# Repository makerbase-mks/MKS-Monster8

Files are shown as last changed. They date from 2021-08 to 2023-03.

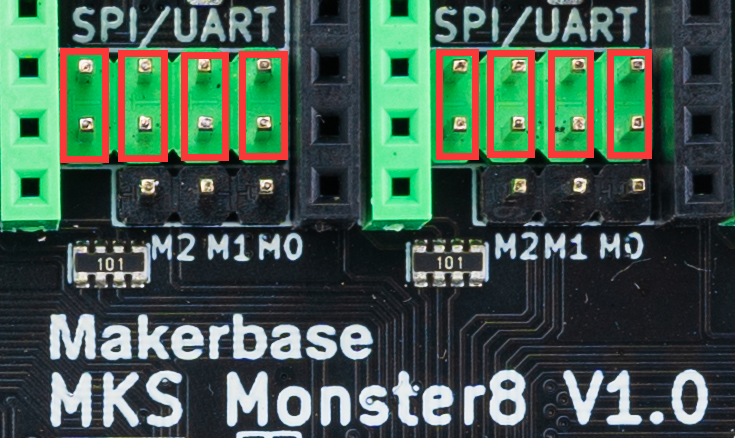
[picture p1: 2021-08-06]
hardware/Image/MKS_Monster8_SPI_set.png

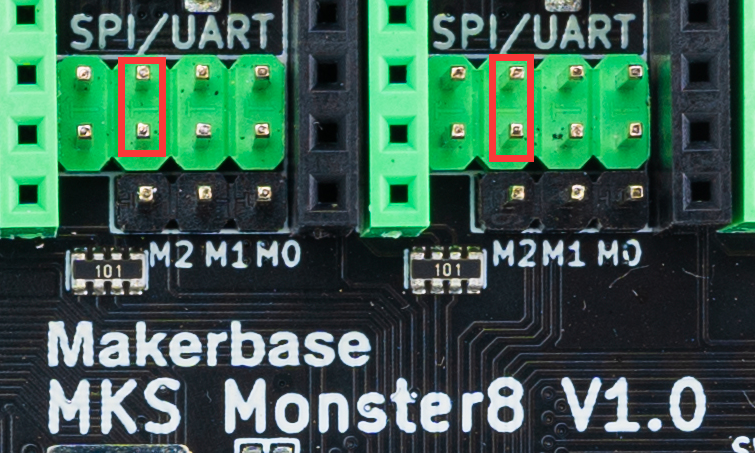
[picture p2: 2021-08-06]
hardware/Image/MKS_Monster8_UART_set.png

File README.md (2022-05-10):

# MKS-Monster8
  Where to buy it?  
  [Monster8 V1 on Aliexpress](https://www.aliexpress.com/item/1005003292898244.html)  
  [Monster8 V2 on Aliexpress](https://www.aliexpress.com/item/1005004241957147.html?spm=a2g0o.store_pc_newArrival.8148356.1.6ecd21f9tROAm6)
  
## Hardware
  - MCU is STM32F407VET6, 168MHz, 512K flash, 192KB RAM
  - DC12-24V input(2 MP1584EN Output DC12V(For FANs) and DC5V)
  - 4 heaters + 4 temps interface(H-BED,HE0,HE1,HE2; TB, TH0,TH1,TH2)
  - 3 PWM FANs + 3 power output(all power can be select by jumper and select VIN, dc12V, dc5V)
  - 8 axis drivers and 9 motor interface(Driver0,1,2-1,2-2,3,4,5,6,7)
  - EXP1,EXP2 support [MKS MINI12864](https://makerbase.aliexpress.com/store/group/LCD/1047297_516922172.html),[MKS TS35](https://www.aliexpress.com/item/1005001446396197.html),LCD12864,LCD2004
  - USART(usart1:PA9,PA10) support [MKS H43](https://www.aliexpress.com/item/1005002008179262.html) or for other serial communication
  - 6 endstop support power select(X-,X+,Y-,Y+,Z-,Z+) and 3D TOUCH(PA8) interface
  - 4K eeprom on board(connect to I2C)
  - Built-in CAN transceiver and interface(connect to CAN)
  - Integrated SPI communication microsd card and reserved SPI signal interface 
  - Integrated UDISK
  - Integrated virtural USB device
  - Support TMC UART and SPI mode, SENSORLESS_HOMING function(Diag0-5,connect to X-,Y-,Z-,X+,Y+,Z+)
  - Support driver power select(5V or 3.3V)
  - Has TVS power spike protection
  - **Possess power reverse connection protection function**
  - Support DFU mode set by button(Boot0)

## Firmware
  - Support Marlin 2.0.x
  - Support Klipper
  - Update firmware
    - DFU upload
	- TF card update
	- Udisk update

## STL files for MKS Monster8 and mini12864 V3.0
You can download from [Github](https://github.com/makerbase-mks/MKS-Monster8/tree/main/STL) or from [Thinkiverse-MKS Monster8](https://www.thingiverse.com/thing:4977292
),[Thinkiverse-MKS Mini12864 V3.0](https://www.thingiverse.com/thing:4918948)
## Related tutorials and Notice
  - MKS Monster8 V1.0 manual, you can refer to Wiki.[click here](https://github.com/makerbase-mks/MKS-Monster8/wiki)
  - MKS Monster8 V2.0 manual, you can refer to Wiki.[click here](https://github.com/makerbase-mks/MKS-Monster8/wiki/MKS_MONSTER8_V2_manual_based_on_Klipper_firmware_to_configure_Voron_2_4_machine)
  - The [marlin 2.0.x firmware](https://github.com/MarlinFirmware/Marlin/tree/bugfix-2.0.x)
  - The [Klipper firmware](https://github.com/KevinOConnor/klipper)
  - [MKS Monster8 klipper firmware bin file](https://github.com/makerbase-mks/Klipper-for-MKS-Boards/tree/main/MKS%20Monster8)

## Note
- Thank you for using MKS products. If you have any questions during use, please contact us in time and we will work with you to solve it.
- For more product dynamic information and tutorial materials, you can always follow MKS's Facebook/Twitter/Discord/Reddit/Youtube and Github. Thank you!
- MKS Github: https://github.com/makerbase-mks  
- MKS Facebook: https://www.facebook.com/Makerbase.mks/  
- MKS Twitter: https://twitter.com/home?lang=en  
- MKS Discord: https://discord.gg/4uar57NEyU
- MKS Reddit: https://www.reddit.com/user/MAKERBASE-TEAM/ 

mks_link

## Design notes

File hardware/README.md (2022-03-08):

# MKS-Monster8-Hardware
- V2.0_003 Version
  - Change it from V2.0_002 Version
  - X-, Y-, Z-, MT-DET interface power only use 5V
  - Z+ power can be select as **VIN** or **5V**, default jump to 5V
  - Version 002 change to 003

- V2.0_002 Version
  - Change it from V1.0_003 version
  - The drive signal is drawn out using the Header 1X4
  - The fuse same as duet2wifi's fuse
  - Endstop, MOS, temperature measurement circuit add schottky diode protection
  - The motor out add Back EMF Protection 
  - X+ pin for MT_DET, Y+ pin for Neopiexl
  - Add MKS Robin Wifi interface
  - E4 axis enable signal same as E0 axis
  - Add MAX31865 interface and the pins use E4 axis
  - Add DC5V 3A out for raspberry pie

- V1.0_003 Version
  - Change it from V1.0_002 version
  - Change D6,D11 packages
  - Power and H-BED interface add silkscreen
  - Optimize U7 design

- V1.0_002 Version
  - Inital version

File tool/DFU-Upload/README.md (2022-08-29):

# MKS-Monster8-DFU
- Upload bootloader
  - Press the Boot0 button when there is no power
  - Connect USB to PC and enter DFU
  - Run: DFU-Upload-Bootloader.bat

- Update firmware
  - Press the Boot0 button when there is no power
  - Connect USB to PC and enter DFU
  - Copy your compiled the mks_monster8.bin file to DFU-Upload path
  - DFU-Upload-firmware.bat
  
- Tips: Can not be modified bootloader's or firmware's file name. Otherwise, DFU cannot be update it.

- More information refer to: https://github.com/makerbase-mks/MKS-Monster8/wiki/DFU_upload

Tip: If your board does not enter the DFU, it may be that the STM32 Bootloar driver is not installed, you can try to run zadig-2.4.exe to install the driver.

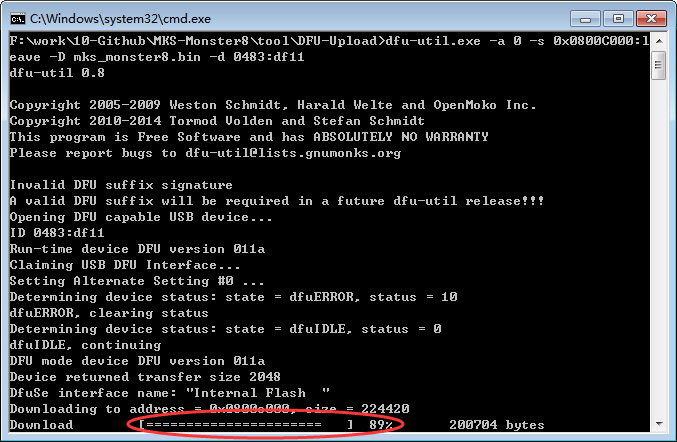
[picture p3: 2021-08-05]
hardware/Image/MKS_Monster8_DFU_upload.png

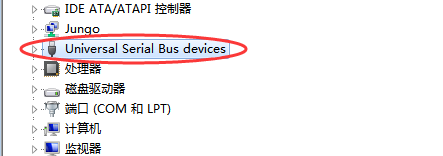
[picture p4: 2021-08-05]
hardware/Image/MKS_Monster8_DFU.png

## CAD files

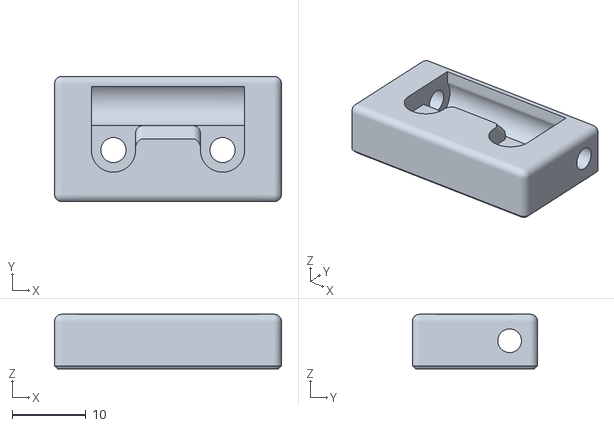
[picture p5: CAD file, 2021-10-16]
STL/MKS Mini12864 V3.0 STL/[a]_mini12864_case_hinge.stl
30.8 x 17.0 x 7.40

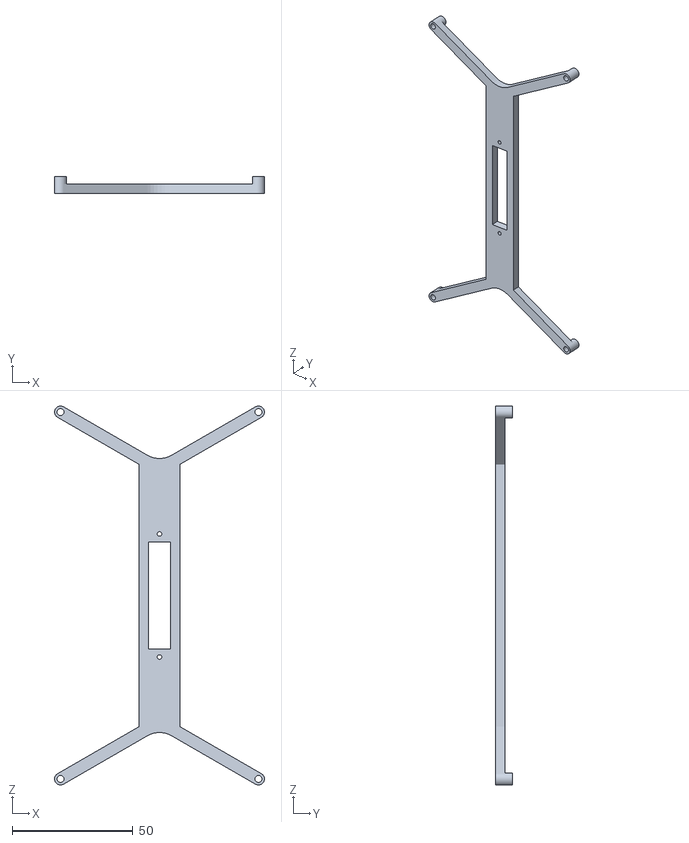
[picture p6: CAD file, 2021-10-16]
STL/MKS Monster8 fixed bracket/Motherboard bracket.STL
87.0 x 7.00 x 157.0

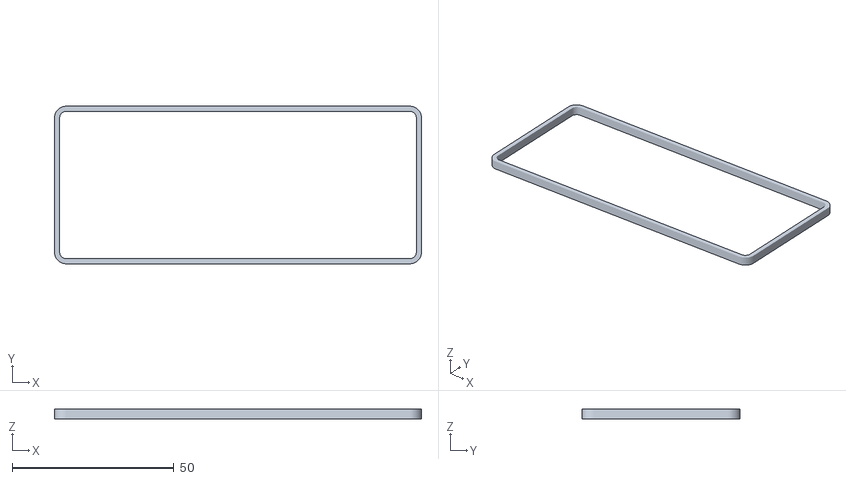
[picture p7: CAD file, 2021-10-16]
STL/MKS Mini12864 V3.0 STL/mini12864_spacer.stl
113.6 x 48.8 x 3.00

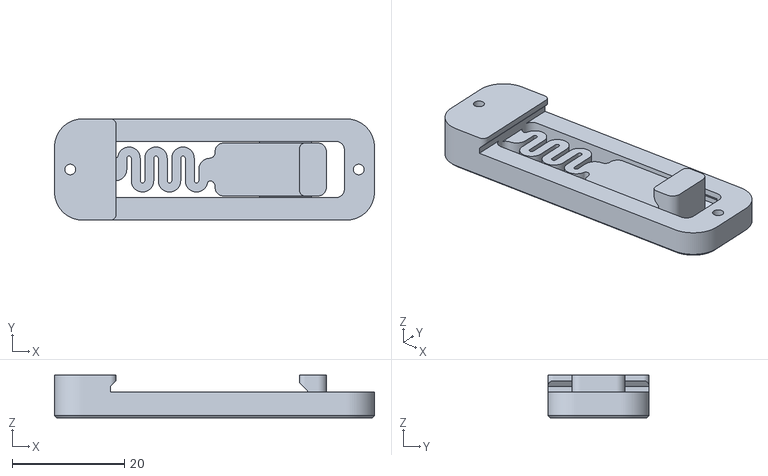
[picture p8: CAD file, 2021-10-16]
STL/MKS Monster8 fixed bracket/pcb_din_clip_x3.stl
56.9 x 18.0 x 7.60

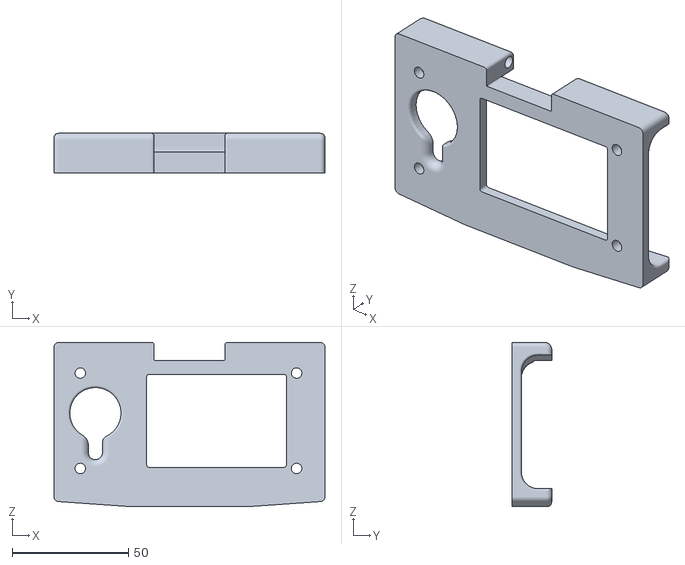
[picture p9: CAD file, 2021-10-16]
STL/MKS Mini12864 V3.0 STL/Upper half.STL
116.5 x 17.0 x 70.6

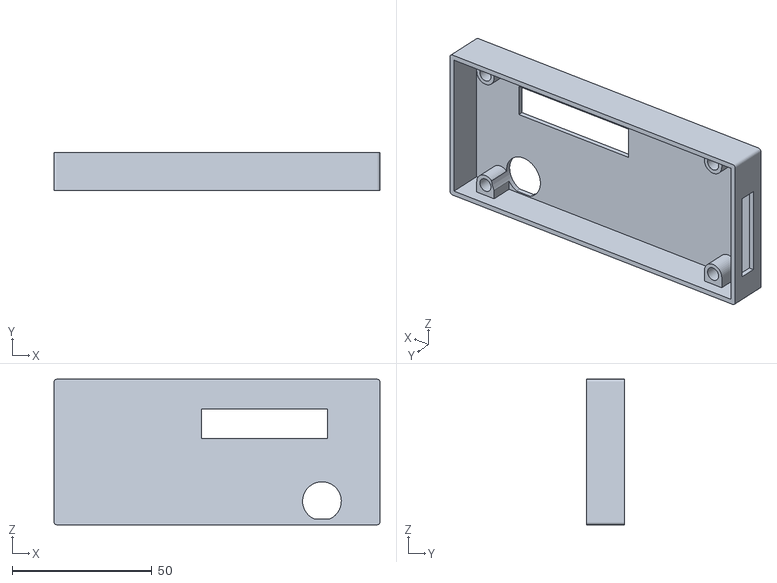
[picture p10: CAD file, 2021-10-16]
STL/MKS Mini12864 V3.0 STL/Bottom half.STL
116.5 x 13.5 x 52.0

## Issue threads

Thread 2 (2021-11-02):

How to connect raspberry?

FabioMiranda10, 2021-11-02:
Is ther a 5v port on the board that supports raspberry pi

mks-viva, 2021-11-05:
I do not recommend that you supply power to the Raspberry Pi directly from the motherboard

mks-viva, 2021-11-19:
V2 has a separate 5V power for raspberry

Diogynes, 2023-06-09:
The V2 5V power supply will not power a Pi over any length of time without under-voltage warnings.  The MP1584E regulator is incapable of sourcing that much current over time.

Closed 2021-11-19.

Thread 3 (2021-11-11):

RRF port support?

whoim2, 2021-11-11:
Goid board with good mcu, but im not find RRF firmware for this

mks-viva, 2021-11-12:
RRF is not currently supported, the main reason is that the memory of 407VET6 is only 512Kb

whoim2, 2021-11-13:
> RRF is not currently supported, the main reason is that the memory of 407VET6 is only 512Kb

fysets adding rrf in f446, 512k flash, see https://github.com/FYSETC/FYSETC-SPIDER/tree/main/firmware/RRF

mks-viva, 2021-11-16:
MKS Monster8 bootloader is 48kb and firmware start address offset is C000, takes up a lot of space.

ShopingLee, 2022-01-10:
will it support rrf in the future, or
 never?

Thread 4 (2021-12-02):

klipper 更新后报错

dflstone, 2021-12-02:
mcu 'mcu': Command format mismatch: config is_config=%c crc=%u is_shutdown=%c move_count=%hu vs config is_config=%c crc=%u move_count=%hu is_shutdown=%c

This type of error is frequently caused by running an older
version of the firmware on the micro-controller (fix by
recompiling and flashing the firmware).

Known versions: host=v0.10.0-169-g520273e5, mcu=v0.9.1-580-g478f26ca

Once the underlying issue is corrected, use the "RESTART"
command to reload the config and restart the host software.
Protocol error connecting to printer

mks-viva, 2021-12-06:
应该是你的配置文件，检查下，或者你直接在MKS Monster8里面下载。

josephchh, 2022-01-11:
可提供連結嗎？

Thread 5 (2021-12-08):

Unable get mcu id

ddpsft, 2021-12-08:
I'm trying to get my mcu id to reach my board using RatOS/Mainsail/Klipper. I'm using the provided bin and cfg files, following klipper's documentation and trying any id I found here, but only having these answers:

18:11:42
Printer is not ready
The klippy host software is attempting to connect. Please retry in a few moments.

18:21:03
mcu 'mcu': Unable to connect
Once the underlying issue is corrected, use the "FIRMWARE_RESTART" command to reset the firmware, reload the config, and restart the host software.
Error configuring printer

Any ideas? I used the same RatOS with a "supported" board and that was much easier.

Klipper and Mooraker log files:
[klippy.log](https://github.com/makerbase-mks/MKS-Monster8/files/7679045/klippy.log)
[moonraker.log](https://github.com/makerbase-mks/MKS-Monster8/files/7679046/moonraker.log)

mks-viva, 2021-12-09:
What you use software and how to get mcu id?

ddpsft, 2021-12-09:
I'm using the provided bin and cfg files for the board and the latest ratOS for the rpi3B+. To get the id I tried to use ls /dev/serial/by-id/* and by-path.
I was using it without a display, just connecting the board to the pi and now I'm trying to do it with connected display to understand what is going in in the board. The first time I updated it was with no display, thus I don't know what happened and now it stucks with "Booting" text for a long time. Then I tryed to flash the bin file again and now it is stuck with "updating 100%" instead of rebooting. My other board (Robin Nano v3) do it and reboots normally, but not the monster8

ddpsft, 2021-12-09:
Fixed that using Putty and SSHing the board, but now I can't go further because apparently the provided bin file is using a old version of klipper (host=v0.10.0-122-gc179db3d, mcu=v0.9.1-580-g478f26ca)

mks-viva, 2021-12-11:
Get MCU id, use 'ls /dev/serial/by-id' command by putty.exe
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

ddpsft, 2021-12-14:
Done. Thank you for your help.

Instead of opening another issue, I'll add one more question. If it's the wrong way, please close the issue and I'll be opening another using the right way.
Is there any documentation about how to edit config.cfg in order to use TS35 display? Monster8's page states that it is compatible, but i've found another issue where was discussed that there is no support. I'm trying do start from the provided voron cfg file (using mini12864) and so far it still showing only "Booting..." on TS35

Closed 2021-12-16.

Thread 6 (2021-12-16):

SPI interface and TS35 display

ddpsft, 2021-12-16:
Is there any documentation about how to edit config.cfg in order to use TS35 display? Monster8's page [here](https://github.com/makerbase-mks/MKS-Monster8) and in [Aliexpress](https://www.aliexpress.com/item/1005003292898244.html) states that it is compatible, but i've found another issue where was discussed that there is no support. I've used the code from generic klipper code and now I'm trying to adapt the provided voron cfg file (using mini12864) and so far it still showing only "Booting..." on TS35.

Additionally, where can I found any detail about pins on SPI3 interface? I'd like to use my adxl345 chip connected to the board instead of connecting to RPi's GPIO pins. The [provided pin "map"](https://github.com/makerbase-mks/MKS-Monster8/blob/main/hardware/MKS%20Monster8%20V1.0_002/MKS%20Monster8%20V1.0_002%20PIN.pdf) doesn't detail it thus I'm no able to identify VCC, G, CS, SDO, SDA and SCL pins.

mks-viva, 2021-12-17:
If you use MKS TS35 for Monster8, you only use marlin 12864 UI or marlin color UI

rafaelnunesdomingues, 2022-07-23:
I have a monster 8 running on a voron 2.4 with marlin. I'm using TS35 which connects to EXP1 and EXP2. How can I implement a Sdcard reader?

Closed 2022-01-11.

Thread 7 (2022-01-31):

Mks Monster8 board firmware flash problem

turnali, 2022-01-31:
Hello,

I just received my monster8 board that I purchased from Aliexpress store. I have been trying to flash the firmware for the klipper for 2 hours but the board doesn't take the firmware. I have even tried marlin firmware but still the board doest take the ''bin'' file. I also downloaded the sample ''firmware.bin'' files from the mks github page to see if those work but still no luck. The board doesnt flash neither klipper nor marlin firmware.
I tried 6 different SD cards( 3 different 128mb,1gb, 8gb, 16gb) to flash but none of them worked.  I am using MKS TMC2209 drivers.
Can you help me please?

DimasVl, 2022-02-01:
What display are you using? What signs indicate that the firmware is not working?

turnali, 2022-02-01:
I am using MKS MINI12864 V3 because of the klipper firmware.
After I flash the klipper firmware, the board never connects to the raspberry pi. And after I flash the marlin firmware, the board never connects to the display.
But most importantly, after I flash the firmwares, I checked the SD cards if the BIN files turned to CUR files but they never do. Everytime they stay as BIN files

turnali, 2022-02-01:
By the way, I also tried BTT TFT35 V3 display but still no luck

DimasVl, 2022-02-01:
Maybe you should try this method? https://github.com/makerbase-mks/MKS-Monster8/wiki/DFU_upload

DimasVl, 2022-02-01:
> Can it be a faulty board?

I don't think the board is faulty. Maybe it's just a bootloader problem and you need to repair it. In this board, this is very easy to do with a usb cable.

DimasVl, 2022-02-01:
I bought Mks Monster8 board and ts_35 display from Aliexpress store a few days ago. First, I configured the marlin firmware with a ts_35 display, uploaded the firmware to a usb flash card. I did not connect anything to the board, even drivers and a display. Then I connected the USB flash with the firmware file, applied power to the board, waited a few minutes and turned off the power. After that, the extension of the mks_monster8.bin file changed (I don’t remember the name of the extension). Then I connected the display and saw the marlin menu on it.
I had a problem with usb and TF card - I could upload the firmware via usb, but on the marlin screen, a usb error was written and there were no g-code files. I spent 2 days to find a setting in marlin that fixed this problem. This setting was not mentioned in the Mks Monster8 manual, I had to spend a lot of time to find it.
Now the board is connected to the printer, 3D Touch is connected, with the TMC2209 drivers, the motors have become silent. I'm very happy ). Here is my short story.)
Maybe I'm not expressing myself clearly - but English is a foreign language for me and I use Google translator.

DimasVl, 2022-02-01:
> I am using MKS MINI12864 V3 because of the klipper firmware. After I flash the klipper firmware, the board never connects to the raspberry pi. And after I flash the marlin firmware, the board never connects to the display. But most importantly, after I flash the firmwares, I checked the SD cards if the BIN files turned to CUR files but they never do. Everytime they stay as BIN files

I forgot to ask which slot you are using for firmware - on the LCD screen or on the board? Do not use the LCD screen's SD slot for flashing. I would advise you to try using a usb flash card and a usb connector on the board. Try uploading the firmware from a USB flash drive, then check if the extension of the firmware file has changed or not. If the extension changes, then you will only need to configure the firmware for your display in order to see the image. I can compile marlin firmware for Monster8 + MINI12864 V3 to make sure the hardware is working.

turnali, 2022-02-01:
> I bought Mks Monster8 board and ts_35 display from Aliexpress store a few days ago. First, I configured the marlin firmware with a ts_35 display, uploaded the firmware to a usb flash card. I did not connect anything to the board, even drivers and a display. Then I connected the USB flash with the firmware file, applied power to the board, waited a few minutes and turned off the power. After that, the extension of the mks_monster8.bin file changed (I don’t remember the name of the extension). Then I connected the display and saw the marlin menu on it. I had a problem with usb and TF card - I could upload the firmware via usb, but on the marlin screen, a usb error was written and there were no g-code files. I spent 2 days to find a setting in marlin that fixed this problem. This setting was not mentioned in the Mks Monster8 manual, I had to spend a lot of time to find it. Now the board is connected to the printer, 3D Touch is connected, with the TMC2209 drivers, the motors have become silent. I'm very happy ). Here is my short story.) Maybe I'm not expressing myself clearly - but English is a foreign language for me and I use Google translator.

Hi,
Your advise about the uploading the firmware via usb flash drive without connecting anything really worked. Its very weird but This should not be the way to flash a firmware very time I need to. Thanks alot about that anyways.
I was able to upload the firmware and the file extension changed to CUR. But I still cannot connect to raspberry pi.
I am using Manisailos and klipper firmware. I am also now using the BTT TFT35 V3 display with this setup.
The board doesnt give serial number from klipper which I using Putty for it but I copied the serial from the mks generic printer.cfg file.
I have tried everything I could to connect the board to the raspbery pi for last 3 hours but although I uploaded the klipper firmware to the board, it just doesnt connect to the Pi.
I am using the type C Usb cable that came with the Monster8 board to connect to the Pi.
From the Mainsail interface, it keeps giving ''mcu'' error.
I just gave up trying now. I am also afraid of damaging the board everytime I unplug all the connections and drivers to upload a firmware trying to fix this problem

turnali, 2022-02-01:
> > I am using MKS MINI12864 V3 because of the klipper firmware. After I flash the klipper firmware, the board never connects to the raspberry pi. And after I flash the marlin firmware, the board never connects to the display. But most importantly, after I flash the firmwares, I checked the SD cards if the BIN files turned to CUR files but they never do. Everytime they stay as BIN files
>
> I forgot to ask which slot you are using for firmware - on the LCD screen or on the board? Do not use the LCD screen's SD slot for flashing. I would advise you to try using a usb flash card and a usb connector on the board. Try uploading the firmware from a USB flash drive, then check if the extension of the firmware file has changed or not. If the extension changes, then you will only need to configure the firmware for your display in order to see the image. I can compile marlin firmware for Monster8 + MINI12864 V3 to make sure the hardware is working.

I was ofcourse using the SD slot on the board not the display. I am not an amateur

DimasVl, 2022-02-02:
> I have tried everything I could to connect the board to the raspbery pi for last 3 hours but although I uploaded the klipper firmware to the board, it just doesnt connect to the Pi.

I've never used klipper and can't offer advice. Pay attention to the klipper configuration, especially the availability of the com port. In the marlin firmware provided by the board manufacturer, the com port is disabled. When it becomes necessary to transfer data to third-party devices, it is necessary to include a com port in the firmware.

turnali, 2022-02-05:
I installed a bootloader to the board. Now the board takes firmware from the sd slot without unplugging anything. And it also gives serial number to connect to raspberry pi and klipper. After lots of hassle, it finally works.
Its interesting that why the board didnt come with a bootloader installed from the factory. Its the first time I see something like this.

makerbase-mks, 2022-02-14:
@turnali Have you change the name of the firmware to be "mks_monster8.bin" before upload?

TrulyMarcus, 2022-10-29:
Can someone please tell me how to upload firmware (or maybe a bootloader) via USB flash drive? My board is no longer noticed by my computer's USB ports.

tranhuunhan82, 2022-12-08:
You can try:
1. Copy firmware .bin to root of SDCard
2. Unplug power of MKS Monster 8
3. Press Boot0 in board
4. Insert SDCard to board
5. Plug Power of board
6. Waitting... to complete

Good luck.

michelspas, 2022-12-16:
On my side it only worked after renaming  Firmware.bin to  mks_monster8.bin.
Then it was OK.
Now I am having problem with the usb to usb-c cable that came with the board.  I am loosing connection.  The printer is stable with my son's similar cable.

Can we use regular USB to regular USB wire to connect to that board?

Dawaitizova, 2023-01-12:
"I had a problem with usb and TF card - I could upload the firmware via usb, but on the marlin screen, a usb error was written and there were no g-code files. I spent 2 days to find a setting in marlin that fixed this problem."

@DimasVl what setting did you use to fix the USB TF card.

marcoslajovic, 2023-08-12:
I managed to put the firmware by doing the following procedure:

1) I connected the MKS Monster board to the PC USB port. The board then appeared in the Windows Device Manager on the COM3 port.
3) I pressed the boot0 and reset buttons on the board at the same time and released it.
4) In the Windows device manager, the board disappeared from COM3 and appeared in Universal Serial Bus Devices under the name of STM Bootloader.
5) I opened the command prompt and entered in the DFU program folder (taken from MKS Monster's github)

cd Users\marco\Downloads\DFU-Upload\DFU-Upload

6) I entered the following command to upload the firmware

dfu-util.exe -a 0 -s 0x0800C000:leave -D mks_monster8.bin -d 0483:df11 dfu-util 0.8

7) The upload was done.

TheMajster007, 2023-10-31:
> Maybe you should try this method? https://github.com/makerbase-mks/MKS-Monster8/wiki/DFU_upload https://github.com/makerbase-mks/MKS-Monster8/tree/main/tool/DFU-Upload

It helped to install the drivers from widnows via zadig.exe, then I ran DFU-Upload_Bootlader.bat. Once I had that installed I copied the firmware.bin file from the raspberry pi and installed it via DFU-Upload-firmware.bat

alucard321pl, 2025-08-21:
I know this is an old issue, but what worked for me was renaming the firmware file to mks_monster8.bin and flashing it from a USB pendrive. I had previously tried several different SD cards, and none of them worked.

It seems like some boards are picky about the storage medium — even though the SD cards were formatted correctly and worked elsewhere, the board just wouldn't recognize them. Using a USB stick solved the problem instantly. Might be worth trying if you're stuck.

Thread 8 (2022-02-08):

USB Drive 'USB start failed'

acguardia, 2022-02-08:
I can't use usb flash drive or multi volume function on Monster 8 Marlin.

Marlin version:
#define CONFIGURATION_H_VERSION 02000902

Configuration_adv.h:
 #define USB_FLASH_DRIVE_SUPPORT
  #if ENABLED(USB_FLASH_DRIVE_SUPPORT)

  #define SDCARD_CONNECTION LCD

#define MULTI_VOLUME
  #if ENABLED(MULTI_VOLUME)
    #define VOLUME_SD_ONBOARD
    #define VOLUME_USB_FLASH_DRIVE
    #define DEFAULT_VOLUME SV_SD_ONBOARD
    #define DEFAULT_SHARED_VOLUME SV_USB_FLASH_DRIVE
  #endif

Configuration.h:
#define SDSUPPORT

Platiformio.ini:
default_envs = mks_monster8_usb_flash_drive_msc

Closed 2022-07-11.

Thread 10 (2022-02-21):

3DTOUCH with MONSTER8 with klipper

selimayaz, 2022-02-21:
Hello, i can't get work 3dtouch with mosnter8. i think i need exact pin names. Can anybody help me? Thnaks.

"
[bltouch]
sensor_pin = PC3
control_pin = PA8
pin_move_time = 0.3
stow_on_each_sample = false
probe_with_touch_mode = false
pin_up_touch_mode_reports_triggered = true
x_offset = -55
y_offset = 0
z_offset = 1.70
samples = 2
sample_retract_dist = 2
samples_result = average
"

BLTouch failed to deploy
Failed to verify BLTouch probe is raised; retrying.
Stats 44.6: gcodein=0 mcu: mcu_awake=0.002 mcu_task_avg=0.000007 mcu_task_stddev=0.000007 bytes_write=7386 bytes_read=8980 bytes_retransmit=9 bytes_invalid=0 send_seq=389 receive_seq=389 retransmit_seq=2 srtt=0.000 rttvar=0.000 rto=0.025 ready_bytes=0 stalled_bytes=26 freq=168001480  heater_bed: target=0 temp=17.9 pwm=0.000 sysload=0.21 cputime=1.272 memavail=1685996 print_time=52.669 buffer_time=0.000 print_stall=0 extruder: target=0 temp=17.0 pwm=0.000
Stats 45.6: gcodein=0 mcu: mcu_awake=0.002 mcu_task_avg=0.000007 mcu_task_stddev=0.000007 bytes_write=7420 bytes_read=9111 bytes_retransmit=9 bytes_invalid=0 send_seq=392 receive_seq=392 retransmit_seq=2 srtt=0.000 rttvar=0.000 rto=0.025 ready_bytes=0 stalled_bytes=8 freq=168001465  heater_bed: target=0 temp=17.8 pwm=0.000 sysload=0.19 cputime=1.287 memavail=1685996 print_time=52.669 buffer_time=0.000 print_stall=0 extruder: target=0 temp=16.9 pwm=0.000
Failed to verify BLTouch probe is raised; retrying.
Stats 46.6: gcodein=0 mcu: mcu_awake=0.001 mcu_task_avg=0.000006 mcu_task_stddev=0.000005 bytes_write=7552 bytes_read=9349 bytes_retransmit=9 bytes_invalid=0 send_seq=400 receive_seq=400 retransmit_seq=2 srtt=0.000 rttvar=0.000 rto=0.025 ready_bytes=0 stalled_bytes=18 freq=168001496  heater_bed: target=0 temp=18.0 pwm=0.000 sysload=0.19 cputime=1.310 memavail=1686264 print_time=52.669 buffer_time=0.000 print_stall=0 extruder: target=0 temp=16.9 pwm=0.000
Multi-probe end
Traceback (most recent call last):
  File "/home/pi/klipper/klippy/extras/probe.py", line 93, in _handle_command_error
    self.multi_probe_end()
  File "/home/pi/klipper/klippy/extras/probe.py", line 102, in multi_probe_end
    self.mcu_probe.multi_probe_end()
  File "/home/pi/klipper/klippy/extras/bltouch.py", line 183, in multi_probe_end
    self.verify_raise_probe()
  File "/home/pi/klipper/klippy/extras/bltouch.py", line 137, in verify_raise_probe
    "BLTouch failed to raise probe")
CommandError: BLTouch failed to raise probe

MKS-hosiey, 2022-03-05:
sensor_pin=!PC3

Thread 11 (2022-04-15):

updating firmware - nothing works

Benster1979, 2022-04-15:
I've tried the following to get it to upload a firmware

SD card - doesn't convert to *.CUR (did it once then on reboot, no longer available)
USB Stick - doesn't convert to *.CUR
DFU-Util - Partially

DFU-Util doesn't appear to work with Windows 10 or 11. Tried on various machines.

Did get DFU-Util on pi to upload both the bootloader and the firmware but it still isn't being detected by the pi outside of DFU mode. "ls /dev/serial/by-id/*" via terminal shows no directories. Doesn't matter if I do make menuconfig or not.

I've tried unplugging screen, drivers and removing the UART jumpers

It never detects the board outside of DFU mode. I've also tried loading the klipper.bin via DFU but still no serial device detected.

Thought I might try your Marlin 2x but it doesn't compile due to errors in features/z-align

Please help

MKS-hosiey, 2022-04-19:
It should be possible to update the firmware with a TF card. Have you checked that your TF card is normal? DFU can work on win10; whether the motherboard is powered by usb to update firmware or switch power supply

MarqSolucoes, 2024-06-21:
I'm having the same problem, what was the solution?

Closed 2022-07-11.

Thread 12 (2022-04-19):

CANbus usage ...

themacboy, 2022-04-19:
It is possible to connect a expansion board like FLY SHT36 board in the Monster8 CANbus port and control this expansion board?

If possible, Can you give a few instructions about how to do it?

Thx in advance !

710920772, 2022-06-06:
hello, you can use MKS USB to Can, And using Usb to connect the board.

tungyao, 2022-08-27:
1. main board need to select `USB to CAN bus bridge` on communication interface optioin
2. SHT board select `CAN bus` option
3.
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

4. `IMPORTANT` If cannot connect the main board , try to manually set baud rate `ip link set can0 up type can bitrate 500000`

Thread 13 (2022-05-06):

MKS Monster8 V2.0_003 SCH.pdf Pinout clarification - correction for Driver4/E0 and Driver7/E5 Enable.

LoganFraser, 2022-05-06:
On the schematic, Driver4/E0 and Driver7/E4 both share PD7, labeled E0-4_EN. On the pinout, Driver4/E0 uses PD7 and Driver7/E4 uses PD14.  Which is correct?  Can you please correct either the schematic or the pinout to reflect the actual enable pin used?  Thank you.

LoganFraser, 2022-05-06:
I must have been on the wrong pinout, my fault. They appear aligned at second view.

Closed 2022-05-06.

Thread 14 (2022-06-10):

DIAG jumpers for Sensorless homing

Sonicboom247, 2022-06-10:
Hello, are the DIAG pins only needed to enable sensorless homing? i am only using sensorless homing on X and Y and BLtouch on Z with TMC 2226 drivers, do I only need DIAG on 0 and 1 or are they needed for anything with a 2226 installed for UART?

MKS-hosiey, 2022-06-11:
Only need to do it on the axis used

Sonicboom247, 2022-06-11:
Thank you for the prompt response

Closed 2022-07-11.

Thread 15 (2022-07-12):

Can you mount the onboard Monster8 MicroSD via the USB-C interface in Marlin?

rondlh, 2022-07-12:
I'm running a recent version of Marlin on a MKS SGEN_L V2.0, it will mount the onboard MicroSD via the USB interface. This makes it easy to update the firmware because I can just plug in the board to my computer and copy the new firmware directly to the MicroSD and reboot to automatically flash the new firmware.

I cannot get this to work on the MKS Monster8 V1.002.
Is it possible to mount the onboard MicroSD via USB on the MKS Monster8 in Marlin so I access the drive on a computer?

rondlh, 2022-07-14:
I still cannot get this to work, Here some more info.
In platformio.ini I select: `default_envs = mks_monster8_usb_flash_drive_msc`
Then a drive letter pops up under Windows 10, but I cannot open it. Also the serial interface stops working, a COM port pops up, but when I connect to it I get a message "Error writing to port". In Marlin I issued an M22 command to release the SD Card from Marlin side (which is working), but still I cannot access the card from Windows. I issue this command via the secondary serial port.
Any suggestion would be greatly appreciated!

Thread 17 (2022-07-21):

Configuration for use MKS H43 on board Monster 8 V2

LoloMake60, 2022-07-21:
Hi,

I would like to connect my MKS H43 screen to the monster 8 V2.

What is the configuration to use USART1?

For Marlin firmware.

LoloMake60, 2022-07-21:
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

MKS-hosiey, 2022-07-22:
#if HAS_DGUS_LCD
  #define LCD_SERIAL_PORT 1
  #define LCD_BAUDRATE 115200

Hello, you only need to configure the serial port to 1 in the advanced configuration, and the others are configured according to H43

LoloMake60, 2022-07-22:
Hi,

Thank you perfect! It works!

I add #define LCD_SERIAL_PORT 1 in the advanced configuration.
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

It works for screen e3v2.
Add line under in pins_MKS_MONSTER8_common.h
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

Thank!

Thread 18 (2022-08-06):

Configuration for use MKS H43 on board Monster 8 V1

satinfo50, 2022-08-06:
Hello to all
I bought a mks-monster8 version one board and a mks-h43 LCD some time ago
Unfortunately, I did all kinds of configuration on the files so that they can be connected to each other through uart, but when I turn it on, only the makerbase logo appears on the screen.
Can someone configure the configuration.h and configuration-adv.h files for Marlin-2.1.x so that this display works on the board?
I tried everything but it didn't work.
i attached my configuration to see what i done
[configuration.zip](https://github.com/makerbase-mks/MKS-Monster8/files/9274486/configuration.zip)
.

LoloMake60, 2022-08-06:
Hi,

I invite you to look at this ==> https://github.com/makerbase-mks/MKS-Monster8/issues/17

satinfo50, 2022-08-06:
Unfortunately, there is no such setting in configuration_adv.h in Marlin-2.1.x

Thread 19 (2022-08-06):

USART 3 on MKS MONSTER 8 V2

LoloMake60, 2022-08-06:
Hi,

I would like to have confirmation on the rt and tx usart3 pins.
RX = PD8 and TX = PD9.
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

Thank you for your confirmation.

mks-viva, 2022-08-16:
PD8 is USART3_TX, PD9 is USART3_RX

mks-viva, 2022-09-03:
Use Klipper firmware?

LoloMake60, 2022-09-03:
no i use marlin

rai0012, 2023-01-31:
Uart3 works for me with marlin

LoloMake60, 2023-02-01:
Hi,

You use usart3 for screen display?

Cordialement,

Le 31 janv. 2023 à 22:07, rai0012 ***@***.***> a écrit :

Uart3 works for me with marlin

—
Reply to this email directly, view it on GitHub<https://github.com/makerbase-mks/MKS-Monster8/issues/19#issuecomment-1411071746>, or unsubscribe<https://github.com/notifications/unsubscribe-auth/AYAWOHXZ5JCNVCUZIRSQFUTWVF5JJANCNFSM55YFZHEA>.
You are receiving this because you authored the thread.Message ID: ***@***.***>

rai0012, 2023-02-02:
Yes, in Marlin and in Klipper.
What I can't get is the wifi to work in Marlin.

LoloMake60, 2023-02-03:
Hi,

Maybe that's it.
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
For me it's works with SERIAL_PORT_1 -1 and SERIAL_PORT_2 1.

rai0012, 2023-02-03:
But the wifi works for you

LoloMake60, 2023-02-07:
Yes the wifi works but the driver 7 E4 it's disable because the jumper move pd11 to wifi.
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
I have flash my mks wifi with ESP3D.
But my screen e3v2 not works, RX and TX on PD9 and PD8.
I don't understand!

rai0012, 2023-02-11:
Let's clarify a bit.
I use marlin I have the dgus screen connected to uart 3 and working, I have the wifi module connected in its slot and it already works for me with flashed esp3d.

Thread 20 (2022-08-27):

USB to CAN bus bridge

tungyao, 2022-08-27:
I flashed the firmware after build ,but cannot find this board both of windows and linux

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

tungyao, 2022-08-27:
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

tungyao, 2022-08-27:
Solved!!

Armbian maybe need to manually set the baud rate ,like this
`ip link set can0 up type can bitrate 500000` and
 first check  the`can0` is connected use `ifconfig -a`

Closed 2024-08-22.

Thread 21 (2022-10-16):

Monster board not noticed after using non-firmware .bin file in sd card slot.

TrulyMarcus, 2022-10-16:
Using a Mac running Monterey. I've never worked with a stm32 board before but have had experience with Arduino boards. I am wanting to use this board because it has 8 stepper axis' and supports most everything else I want to do, but I don't want to use Marlin or Klipper. I want to write and upload my own code like I would a Mega 2560.

I downloaded and installed the stm32 board library in the Arduino IDE. I would plug in with the USB, open the Arduino IDE and the monster board would give a read out in serial monitor about the different parts of the board but I could never upload to it, I tried each of the options under Upload Method.
All the guides say load the monster8 firmware to a microsd card with the firmware file named mks_monster8.bin. I made a super simple serial print program in Arduino, exported to be .bin and renamed it mks_monster8.bin. When I put that in the board and hooked it up to the computer it is no longer recognized in any of the USB ports. Neither Arduino or the Stm32 programmer see anything there anymore.

I'm guessing I need a USB to TTL connection to upload a Bootloader (like here https://www.mischianti.org/2022/06/20/stm32-programming-stm32f1-stm32f4-via-usb-with-hid-boot-loader-3/) so I can start uploading code. But the Monster pinout doesn't show the A10 or A9 pins that the guide talks about. But I'm hoping someone with more knowledge could even tell if that is the solution.

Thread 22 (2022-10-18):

About protection circuit

tungbuivn, 2022-10-18:
Here is protection for the hotbed temp
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

if for some reason, the 24v going to pin 1 of j26, then every circuit is protected by the zenner D46-1, it will make sure voltage is 3.3v, but the power of zenner only 50mW, and the massive current from 24v will destroy zenner D46-1, so the circuit become unprotected and 24v will replace power source 3.3v, can it burn our board ?

blackwi7ard, 2025-06-21:
well, Fan number 0 on my board shorted out and the entire board burned out.

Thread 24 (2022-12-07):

外接驱动时，跳帽设置

leon-titan, 2022-12-07:
1. 当外接驱动时（如雷赛 m542 驱动），跳帽是否是按 A4988 设置？
2. 雷赛 m542 本身可以设置细分，怪兽主板上的细分设置是否还起作用？
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

mks-viva, 2022-12-07:
你引出去的只是驱动信号，细分，电流都是由驱动器本身设置

leon-titan, 2022-12-07:
> 你引出去的只是驱动信号，细分，电流都是由驱动器本身设置

所以外接驱动时，怪兽主板上的跳帽随便怎么都不影响是吗

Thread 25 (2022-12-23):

mks robin wifi

mozg4D, 2022-12-23:
failed to make mks robin wifi to work with mks monster 8
failde to make MKS TS35 V2 to work in TFT_LVGL_UI mode
need manual

mozg4D, 2022-12-24:
Seems like: in order to run wifi, one need tft screen in LVGL UI mode.
The only supported tft screen is TS35, which requires SPI flash to run in LVGL mode, which is missing
So.. is wifi (mks cura plugin) impossible on monster8?

marcoslajovic, 2023-08-12:
I would also like to make the WIFI module work on the monster board. I thought about the possibility of connecting a TFT display that has support for the WIFI module on the Monster, but unfortunately the board does not have the AUX1 connector, only the EXP1 and EXP2 connectors. Is it possible to make a TFT touch display work on the Monster?

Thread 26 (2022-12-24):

V2 board starts burning when attempting dfu mode

boannarrow, 2022-12-24:
My monster8 v2 starts burning on the marked piece after holding the boot button while the board is off and turning it on with the button pressed. I'm trying to add marlin binary file transfer via octoprint. Marlin 2.1-bugfix. My ras-pi and my computer see my board as a com port but the .bat files don't run and dfu-utils isn't recognizing my device.
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

MKS-hosiey, 2022-12-29:
you can  copy the mks_monster8.bin file to the TF card, and you can update it with the card, or update the .bin file through dfu

casiobearing, 2023-01-23:
I would like to confirm this "V2 board burning" issue - What bonnarrow means is that when you put the Monster8 board into DFU mode, HE-0 is enabled (the red LED turns on), causing Extruder0 to begin heating. There could cause a hot end fire if the board remains in DFU mode for an extended period of time.

casiobearing, 2023-02-02:
In the end I think Q7 MOSFET was a faulty component from manufacturer. Not good ;O(
Got naff all help from the Monster8 supplier so I repair the board myself by replacing Q7 MOSFET with a equivalent one and also changed MOSFET drive signal from PB10 to PA8. This just needed removing of the 100Ohm SMD resistor situated near the external drive jumper.
I'm going to be using a 240VAC mains powered bed heater anyway which is way more efficient and this will take the strain off the bed heater circuitry - using high power MOSFETs for this application isn't a good idea.

Anyway the repair is working and entering DFU mode doesn't cause problems any more.

FauthD, 2023-07-13:
Well, I do not think this is a faulty device. To much coincidence for this many cases.

For Q7 the situation in DFU is the same as in normal bed heating (if 3.3V is applied from the TX3).
Perhaps the ouput of TX3 (PB10) is much less (1.8V ?), leading to a partially switch on situation that heats up Q7 until it dies.

Just my guess after 50 years of experience in electronics.

masapod2892, 2024-04-09:
Just encountered the same issue on the v1 board but in a different scenario. When I was heating the bed up to do my first print I smelled something burning then to my surprise the mosfet was hot enough to desolder itself.

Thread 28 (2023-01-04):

Monster8 v2 H43 Wifi

rai0012, 2023-01-04:
Hello, how can I connect the mks H43 screen and the MKS Robin wifi module and make it work.
If I connect the screen to uarts 1 and the wifi module does not work since they use the same one.
Does the board have more uart ports?
I use marlin 2.1.2
thank you

rai0012, 2023-02-06:
I already got it thanks for nothing

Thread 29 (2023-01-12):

Monster 8 USB/sd card not working in firmware

Dawaitizova, 2023-01-12:
Monster 8 USB/sd card not working in firmware(I can fash firmware still via ethier) . This must be a setting in Marlin but I can't figure out which one it is

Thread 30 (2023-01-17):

Modifying Monster8-v2 for entering BOOT0 mode via remote pushbutton

casiobearing, 2023-01-17:
Some 3D printers have controller boards buried deep within their structure so they are not accessible without dismantling the entire printer. This is fine if you are using the Arduino IDE firmware update mechanism via USB as it all worked automatically. However with the Monster8 board if you want to use STM32CubeProgrammer via the USB C interface this requires putting the board into boot0 mode by physically pressing the boot0 pushbutton. The modification described below replaces the pushbutton with a 2 pin header allowing a button to be positioned where it is easily accessible.

Start with a standard 3x2 pin right-angled male header and remove all the metal pins. Then cut down two of the longer right angled pins such that their length matches the SMD pads for the pushbutton. Trim the bottom edges of the header plastic to ensure it sits flush to the board when the pins are re-inserted for mechanical stability. Then pre-tin the pins ready for mounting on the board, unsolder the pushbutton, re-tin the SMD pads and then solder the new header in place. :o)
Using a standard soldering iron instead of a hot air gun avoids disturbing any nearby SMD components.

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

Closed 2023-01-21.

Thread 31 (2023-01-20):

CPU Pin PB11 missing from MKS Monster8 V2.0_003 SCH Schematic Diagram

casiobearing, 2023-01-20:
Hi,

I believe that PB11 is missing off the schematic diagram for U1, and that it should be connected to the wire labelled SPI1_DET.

Thanks :o)

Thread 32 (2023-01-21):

How to - Visual Code, STM32CubeProgrammer, compiling Marlin and upload via USB C DFU Boot0 method

casiobearing, 2023-01-21:
Here's how to upload firmware to Monster8 using STM32CubeProgrammer via the USB C connection.

Install Visual Code and then add in the extensions for PlatformIO and "Auto Build Marlin".
Download the Marlin source code zip file from github and unzip it somewhere accessible for Visual Code.
Now find in that unzipped code the file in folder "Monster8\Marlin-2.0.x\ini" called "stm32f4.ini"
You want to edit that file to change lines 410, 411 to read as follows -->
board_build.offset          = 0x0000
board_upload.offset_address = 0x08000000

Now use Visual Code to compile (using Marlin AutoBuilder works fine for this) using the environment called "mks_Monster8".
The compiled file will be found in folder "Monster8\Marlin-2.0.x\.pio\build\mks_monster8" and it will be
called either "firmware.bin", "firmware.elf" or "mks_monster8.bin"  (you can use either of them for the following download process).

Attach your Monster8 board to your computer via its USB C socket (you can't use the USB 2.0 connector for this activity).
Press and hold down the "Boot0" button and either power on the Monster8 board or press and release the "Reset" button.
Your computer should then detect a USB device has arrived - It will be show right at the bottom of Windows "Device Managers list", called "STM32 BOOTLOADER".

Run up STM32CubeProgrammer, in the top right corner, select "USB" and click "Connect". This will connect to the Monster8 board and show details about the STM32F407 processor. In STM32CubeProgrammer, Open File to the "firmware.bin" file from above, and then click "Download" to send it to the Monster8.
Then just reset or reboot your Monster8 board to get your new code up and running.
Hope this helps anyone stuck trying to get things going :o)

casiobearing, 2023-01-28:
I should warn you that if you use decide to use BOOT0 DFU mode, that you should physically disable your heat bed (e.g. by removing fuse FS1) before entering DFU mode. See issue #26 if in doubt why.
I have modified my Monster8 board to change the MOSFET Q7 gate drive signal. I disconnected PB10 (by removing the 100 Ohm resistor) and connected the MOSFET gate to PA8 (used for 3DTouch). This modification stops the hotbed from heating up when you go into DFU mode.

gitcnd, 2024-12-06:
For the curious, I do not think this works on the Monst8 V2 (I guess they are using emulated USB, and not native serial now?):

Windows no longer detects anything when the board goes into DFU mode.

The SWD pins do work to load and backup firmware using j-link at least.

This pinout is confirmed working for that:
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

HattonLe, 2024-12-06:
I use a real USB port on my Dell M6700, and Windows running baremetal i.e. no VM.

Closed 2023-01-28.

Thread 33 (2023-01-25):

Bootloader without beep

30350n, 2023-01-25:

30350n, 2023-01-25:
Hey! Would it be possible to get a bootloader that doesn't trigger the beeper, similar to the one that exists for the [MKS-Robin](https://github.com/makerbase-mks/MKS-Robin-E3-E3D/issues/35)?

LaRenard, 2023-04-04:
I would also like to be able to disable the beep, when I restart klipper it beeps every time and I'd prefer the option to disable this.

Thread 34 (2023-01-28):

LCD Screen corruption on certain config builds based on the given pins Monster8.h file

casiobearing, 2023-01-28:
Occasionally my REPRAP SMART FULL DISCOUNT CONTROLLER  LCD screen would completly garble on some rebuilds of this code base whislt porting it to my hardware.

I found issue https://github.com/MarlinFirmware/Marlin/issues/21778 which point me to the required LCD screen fix.
I used the following changes to fix the problem  -->
    #define BOARD_ST7920_DELAY_1    DELAY_NS(125)
    #define BOARD_ST7920_DELAY_2    DELAY_NS(85)
    #define BOARD_ST7920_DELAY_3    DELAY_NS(600)

casiobearing, 2023-01-28:
It only takes a minor config change sometimes to cause the problem, in my case it was just adding in a KILL_PIN.

Closed 2023-01-28.

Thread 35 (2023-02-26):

USART in MKSPI

leorpereira87, 2023-02-26:
Hello,
forgive me my English.
I recently purchased an MKSpi, and I would like to communicate with the Monster8 using the USART, has anyone tried this, and was it successful?
Currently I am using Kleeper and connecting via USB-c

rafdekar, 2023-03-29:
Hi there, I am using this configuration. To make it work you need to follow Klipper instructions [here](https://www.klipper3d.org/Installation.html) to create new motherboard image with UART enabled. After that just use this mcu config in your printer.cfg
`[mcu]
serial:/dev/ttyS0`

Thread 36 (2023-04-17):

Unknown spi_bus 'spi4' - klipper

proturka, 2023-04-17:
I am trying to install TMC5160-HV to my monster8 v2 card. I installed everything like the klipper sample config file.

But when i want to save and restart it, i am getting this error. Can you help me to figure it out whats happening?

Card is working well, also UART mode works well with TMC2209. SPI mode is not working.

rexshamhk, 2023-05-13:
Same issue here. I used TMC5160-PRO from BIGTREETECH
Searched all the documents and copying the config from this file [https://github.com/makerbase-mks/MKS-Monster8/blob/main/klipper%20firmware/generic-mks-monster8.cfg](url) just yields the  "Unknown spi_bus 'spi4' " error...

These settings are just wrong
#[tmc2130 stepper_x]
#spi_bus: spi4
#cs_pin: PE6
#diag1_pin: PA14
#run_current: 0.800
#hold_current: 0.500
#stealthchop_threshold: 999999

#[tmc2130 stepper_y]
#spi_bus: spi4
#cs_pin: PE3
#diag1_pin: PA15
#run_current: 0.800
#hold_current: 0.500
#stealthchop_threshold: 999999

#[tmc2130 stepper_z]
#spi_bus: spi4
#cs_pin: PB7
#diag1_pin: PB13
#run_current: 0.800
#hold_current: 0.500
#stealthchop_threshold: 999999

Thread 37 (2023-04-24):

MKS Monster8 v2 max amp for neopixel

TheSin-, 2023-04-24:
I can not find info for max amps on the 5v rail.  I tried to run a cm4 off the pi port but kept getting under voltage so I assume it’s less than 3amps.  Now I’d like to run 2m of neopixel 60 which will need 1amp per meter.  There is nothing else on the 5v rail is there 2amps avail?

TheSin-, 2023-04-28:
Also have anyone gotten the neopixel pin to work with klipper?  I added an external PSU to make sure I had enough 5v, but I still can not get any lights to turn on at all :(

```
[neopixel chamber]
pin: PC5
chain_count: 102
color_order: GRBW
initial_RED: 0.0
initial_GREEN: 0.0
initial_BLUE: 0.0
initial_WHITE: 1.0
```

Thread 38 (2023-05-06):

LED of StealthBurner not working

DaTTcz, 2023-05-06:
Hello, I connected the stealthburner LEDs to the PC5 port (neopixel) but they don't work here. In the sample configuration, port PA9 is used for the LEDs and PC5 for the motor. I don't see PA9 on the board in the pinout documentation. What am I doing wrong ? So which port is for the stealthburner LED ?

Closed 2023-05-06.

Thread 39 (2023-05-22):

Phaetus Rapido 24V Monster 8 v2

canadank0, 2023-05-22:
Hi guys,
I installed Phaetus Rapido hotend on my Monster 8 board but i cannot make it heat it up properly, looks like  HE0 is just 12V. how can i feed 24V to my new rapido?

thanks Daniel

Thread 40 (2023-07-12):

Bed is always heated after upgrade FW to v0.11.0-241-gffb5105b

FauthD, 2023-07-12:
Hi,
with FW mks_monster8 v0.10.0-557.bin my Sermon D1 worked just fine regarding the bed.
Since the neopixel did not work properly (looks like a timing issue), I tried the latest FW compiled locally.
Did a make menuconfig and double checked the values agains the readme.md.
Compiled with `make clean` followed by `make`.
Then flashed with
`make flash FLASH_DEVICE=/dev/serial/by-id/usb-Klipper_stm32f407xx_39003E001250304B56333920-if00`
(Stopped the klipper service for this).

Now the bed gets heated right after reboot until the emergency shutdown occurs.

Do you know about any changes that could cause this?

MKS-hosiey, 2023-07-20:
R38 100 Ω，R40 100kΩ，Q7

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
R38 100 Ω，R40 100kΩ，Q7  HYG024N03LR1D  TO-252

FauthD, 2023-07-30:
Hi,
The official MKS-Shop at Aliexpress provided me with the correct transitor (I had to pay 1.08€). Replacing it was not too bad with my cheap hot-air station. Better would be some heating underneat the board, but it worked out well.
Now the board works fine again.

Trying to find the root cause did not expose something:

1. Disconnect the bed heater just in case.
2. Flash the original FW from this github page. (V0.10.x)
3. Reboot
4. Update to latets FW with "make flash ...".
5. Measure the gate voltage of Q7 with Oscilloscope. It was zero all the time, so the Q7 should not have been turned on (or partially turned on as I suspected).
6. Do the same again with the latest FW (V0.11.x), same result.
7. If bed needs heat, the Gate voltage is 3.3V.

So I cannot explain the issue, though I do not believe it was pure coincidence.
I recommend to disconnect the heater bed while DFU, or just use the USB supply.

PS: I think R40 is only 10K, not 100K as MKS-hosiey mentioned.

Regards, Dieter Fauth
1.

1.

FauthD, 2023-07-30:
Solved and close.

FauthD, 2023-07-30:
Solved and close. (second try to close)

Closed 2023-07-30.

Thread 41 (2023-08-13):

Using MKS TFT35 display in MKS Monster8 V2

marcoslajovic, 2023-08-13:
I've been looking for the last few days how to use a MKS TFT35 touch screen display on the MKS Monster8 board without success. I finally figured out how to do it so I decided to create this post.

On the MKS TFT35 display, connect a 4-pin cable to the AUX-1 connector on the 4 lower pins where it says TX RX GND +5V.

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

On the Monster8 board, connect the same cable with the same sequence to the UART connector (next to the CAN I2C connectors). In this connector, the pins are in the sequence from top to bottom like this: RX1, TX1, GND and +5V.

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

The TX pin from TFT35 display must be connected to the RX1 pin in monster board, the RX pin in TFT35 display must be connected to the TX1 pin in TFT35 board.

In Marlin 2.0 firmware in config.h set serial_port2 equal to 1:

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

In the variant.h file that is in the folder: buildroot/share/PlatformIO/variants/MARLIN_F407VE
Change the serial_uart_instance to 2:

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

With this change, the UART connector on the board becomes Serial2 (USART2), which will connect to the Serial_port_2 configured in config.h. Serial_Port_2 receives the value 1 to say that it is the first serial port on the board, although it already has a serial port but which is defined by default at -1 to make the connection with the PC.

The following photo shows the system working with the display reading the plate temperature sensor.

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

guesch39, 2024-07-06:
Hello,
I did the same combo with the MKS TFT35 V1 on my Monster 8 V2 and it works perfectly. I have the BTT Firmware ( MKS_TFT35_V1_0.27.x_encrypted.bin ) and it works perfectly.
However, when I plug the WIFI module on my lester 8 V2 the connection between the screen and the card does not work.
I know that the wifi module uses uart 1 and the screen too.
How can I resolve this conflict?

LucasCarapella, 2024-10-17:
@guesch39 Hi, were you able to solve this problem?

guesch39, 2024-10-17:
Hi, no the problem is present, I unpluged the MKSWIFI !

LucasCarapella, 2024-11-01:
Hola, @marcoslajovic @guesch39
¿cuando pongo a calentar el extrusor calienta, pero no se actualiza el valor de la temepratura actual, tuviste este problema?

Es como si la madre recibiera la información de calentar, pero esta no le informa a la pantalla a que temperatura está. Ya modifique y probe valores en el puerto serie, y en la configuración del buffer seri

LucasCarapella, 2024-11-01:
Hello, @marcoslajovic @guesch39
When I heat up the extruder it heats up, but the current temperature value is not updated. Did you have this problem?

It's as if the mother receives the heating information, but it doesn't inform the screen what temperature it is at. I've already modified and tested values   in the serial port, and in the serial buffer configuration.

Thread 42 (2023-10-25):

What is component D3 on the V2

CallmeJohnny, 2023-10-25:
D3 decided to blow up, ive double checked my wiring and everything looks fine. What is the name/part number so i can replace it.

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

Closed 2023-10-26.

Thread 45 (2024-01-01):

Sensorless homing for x & y

kvng1, 2024-01-01:
I have TMC2209 on uart mode for x & y drive. Do I need 3,3V or 5V on drive ic- pwr jumper to use sensorless homing? I'm using klipper.

alfadhela, 2024-09-27:
Yes you need to set ic-pwr jumper to 3.3v.
https://github.com/makerbase-mks/MKS-StepStick-Driver/tree/master/MKS%20TMC2209

juniortada, 2025-07-27:
Work for me using 3.3v with marlin.
STALL_SENSITIVITY in 150
TMC2226

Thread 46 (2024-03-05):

MKS Monster 8 V2 and TS35V2 HELP

Startbh, 2024-03-05:
[Error.txt](https://github.com/makerbase-mks/MKS-Monster8/files/14499569/Error.txt)
[Configuration.txt](https://github.com/makerbase-mks/MKS-Monster8/files/14499582/Configuration.txt)
[Configuration adv.txt](https://github.com/makerbase-mks/MKS-Monster8/files/14499614/Configuration.adv.txt)

Hi I need help I simply do not see a place where is error. I am making dual Z DIY printer. Can anybody check where is error?

MKS Monster 8 V2
MKS TS 35V2

ellensp, 2025-05-16:
The error message is clear "Z_STEPPER_ALIGN_KNOWN_STEPPER_POSITIONS requires NUM_Z_STEPPER_DRIVERS to be 3 or 4."

You enabled the following

```cpp
// Requires triple stepper drivers (i.e., set NUM_Z_STEPPER_DRIVERS to 3)
  #define Z_STEPPER_ALIGN_KNOWN_STEPPER_POSITIONS

```
But you ignored  the comment right above it

You only have 2 Z stepper drivers enabled.
So you CANNOT enable this feature.

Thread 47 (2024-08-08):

pwm fan out

selimayaz, 2024-08-08:
Hello, i want to use roborock fan as part fan. it requires PWM pin and i couldn't see which pin i can use. The project link is belove. Thanks.
https://github.com/condottab/Roborock-CPAP

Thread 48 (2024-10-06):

make参数不正确

ss22219, 2024-10-06:
https://github.com/makerbase-mks/MKS-Monster8/blob/0116434039f06b17c72ed5d1c43724a9d4a5d81b/klipper%20firmware/README.md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

make: *** No rule to make target 'menufconfig'.  Stop.

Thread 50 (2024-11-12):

Monster8 v2.0 Neopixel pin(PC5) not working

ivantem86, 2024-11-12:
Hi
Voron的Stealthburner, 使用三顆連接的SK6812, 不點亮
已進行過的排查:
1. 同一串LED接到Arduino測試, 卻可以點亮, 並可依指令變色.
2. 在Stealthburner的空中接頭處使用電表測量, +5v, 且正負極的接線無誤
3. 在靠近主板的data線, 接上100歐姆電阻, 仍不點亮
4. Mainsail控制介面中, 有列出兩個neopixel, 分別是min12864與sb_leds(表示config有被讀入), 前者可點選顏色變色, 後者卻無反應.
5. 確認config中, pin: PC5, 符合官方PIN diagram對此pin的編號. color_order則是RGBW與GRBW都試過了仍無效

請問, 是否應將SK6812的data線拉到其他pin, 或者還有進一步偵錯的手段?
謝謝
Ivan

kwankiu, 2024-12-08:
Same here with WS2812B Neopixel, PC5 doesn't work, as a workaround, I connected it to the 3DTouch Pin PA8 instead.

ivantem86, 2024-12-19:
> Same here with WS2812B Neopixel, PC5 doesn't work, as a workaround, I connected it to the 3DTouch Pin PA8 instead.

Yes, I also found PA8 is alternative, I posted this finding on discord but forgot to reply myself on this github post. thank you for posting the solution.

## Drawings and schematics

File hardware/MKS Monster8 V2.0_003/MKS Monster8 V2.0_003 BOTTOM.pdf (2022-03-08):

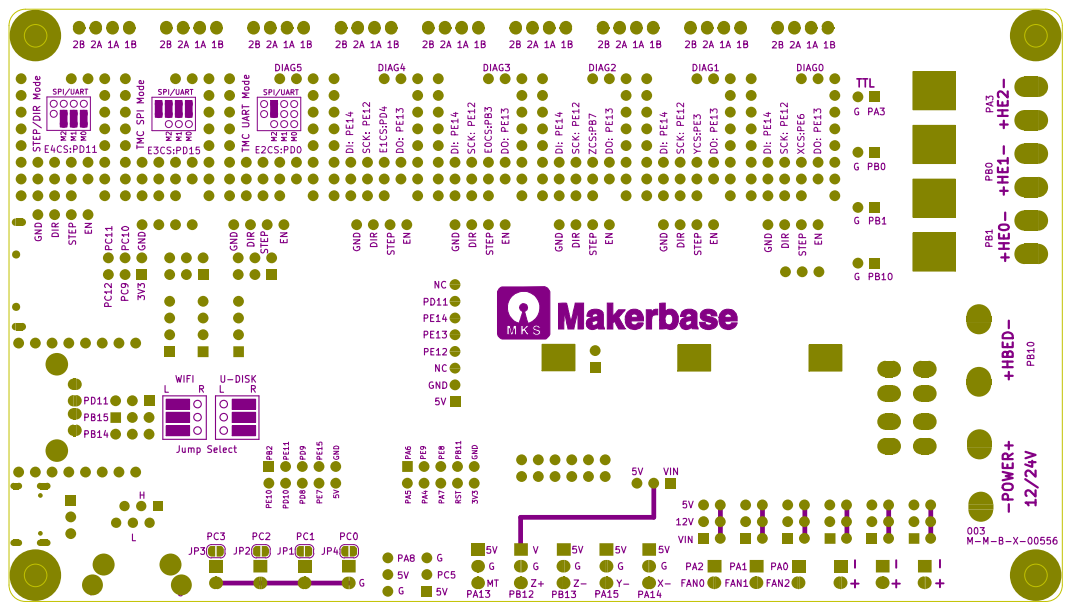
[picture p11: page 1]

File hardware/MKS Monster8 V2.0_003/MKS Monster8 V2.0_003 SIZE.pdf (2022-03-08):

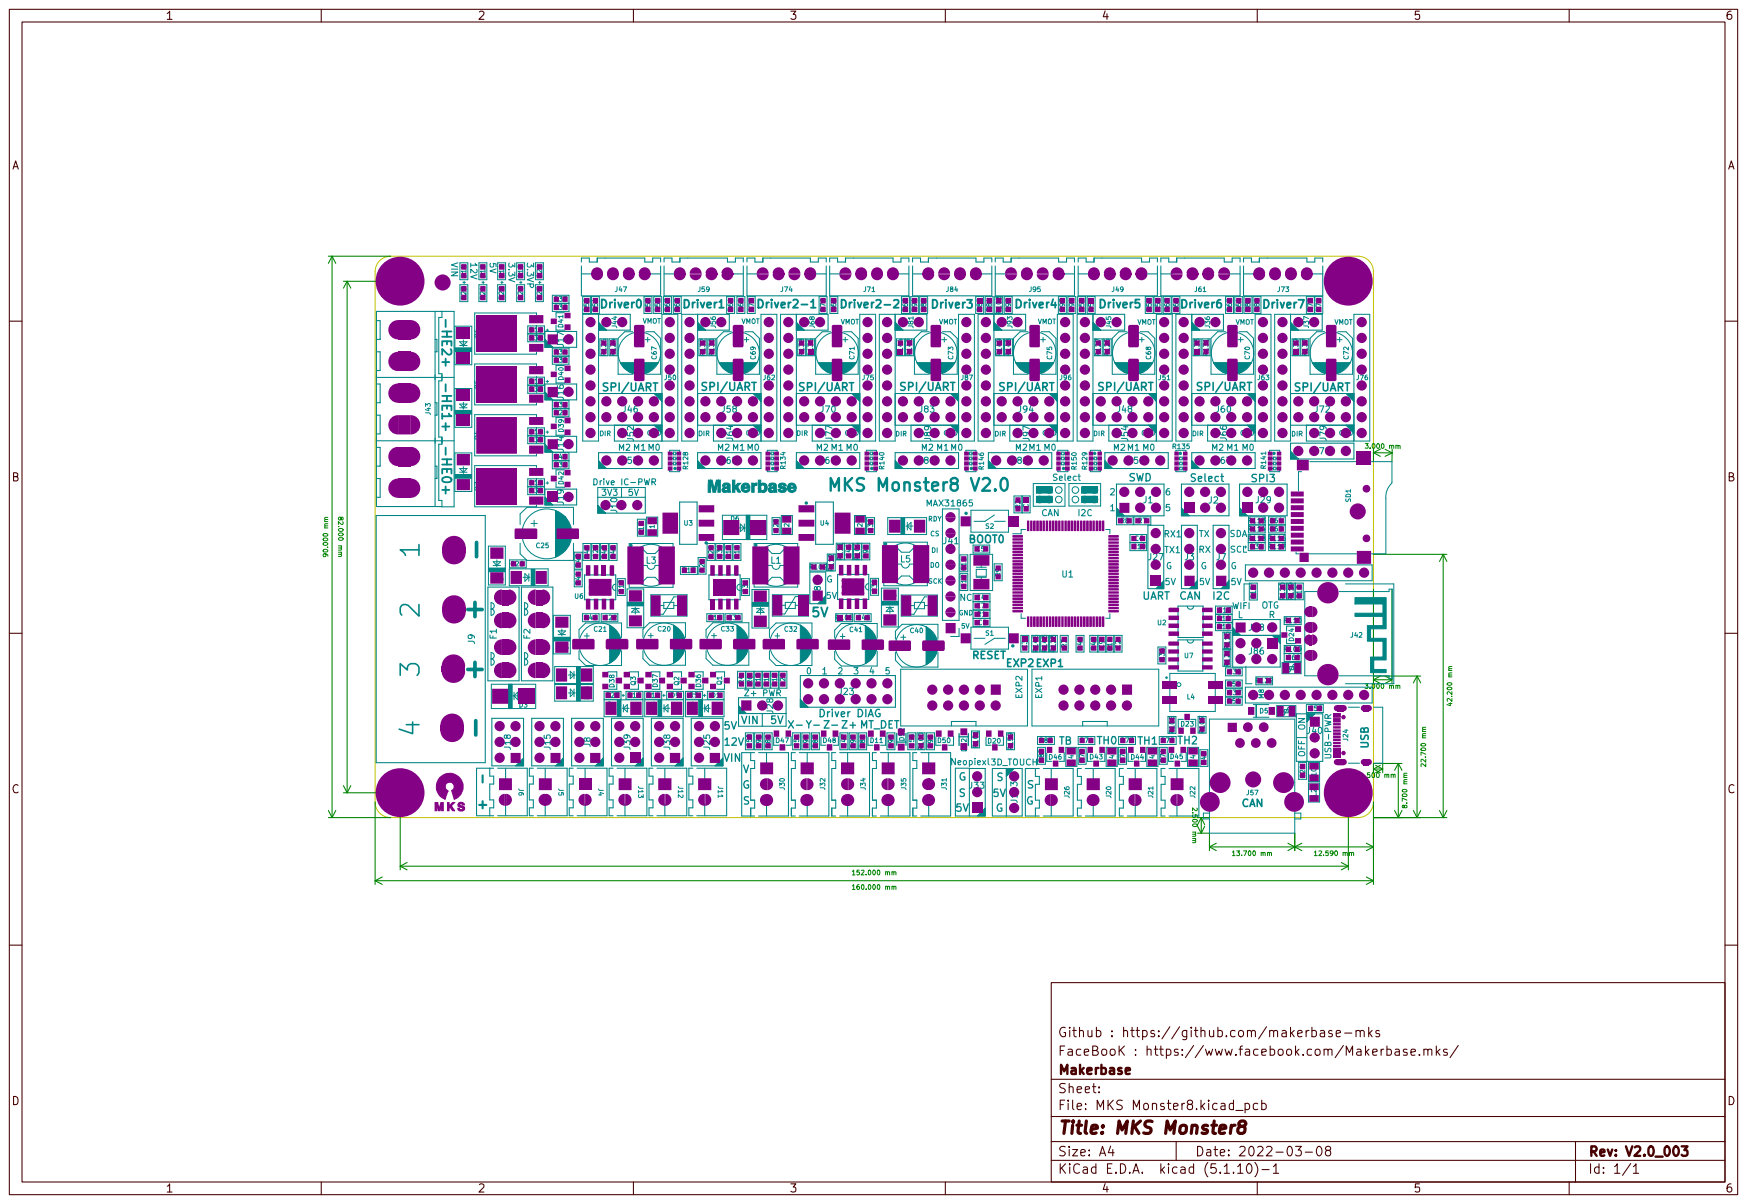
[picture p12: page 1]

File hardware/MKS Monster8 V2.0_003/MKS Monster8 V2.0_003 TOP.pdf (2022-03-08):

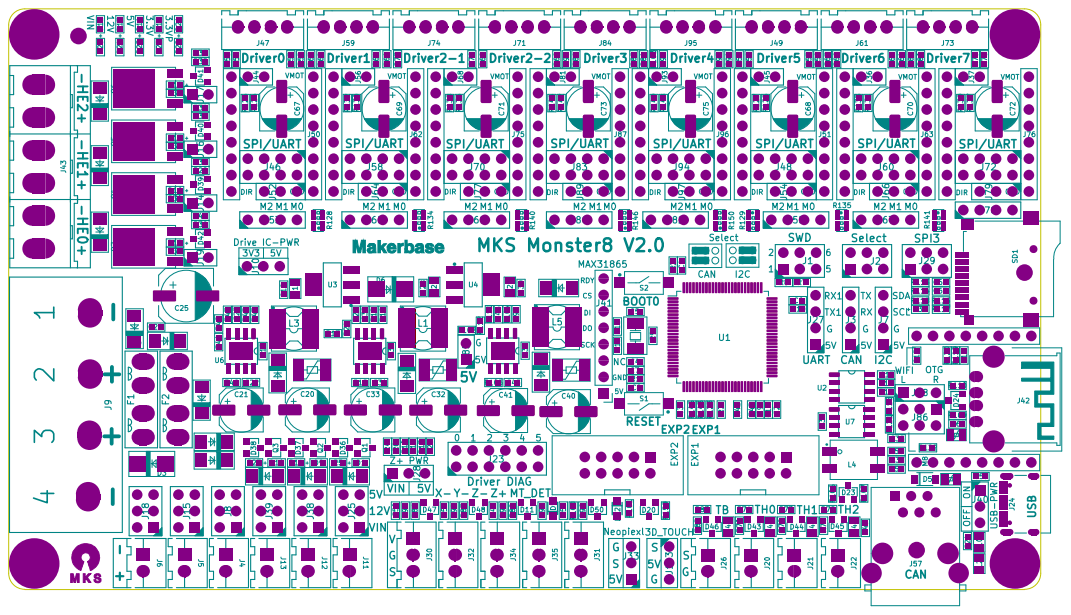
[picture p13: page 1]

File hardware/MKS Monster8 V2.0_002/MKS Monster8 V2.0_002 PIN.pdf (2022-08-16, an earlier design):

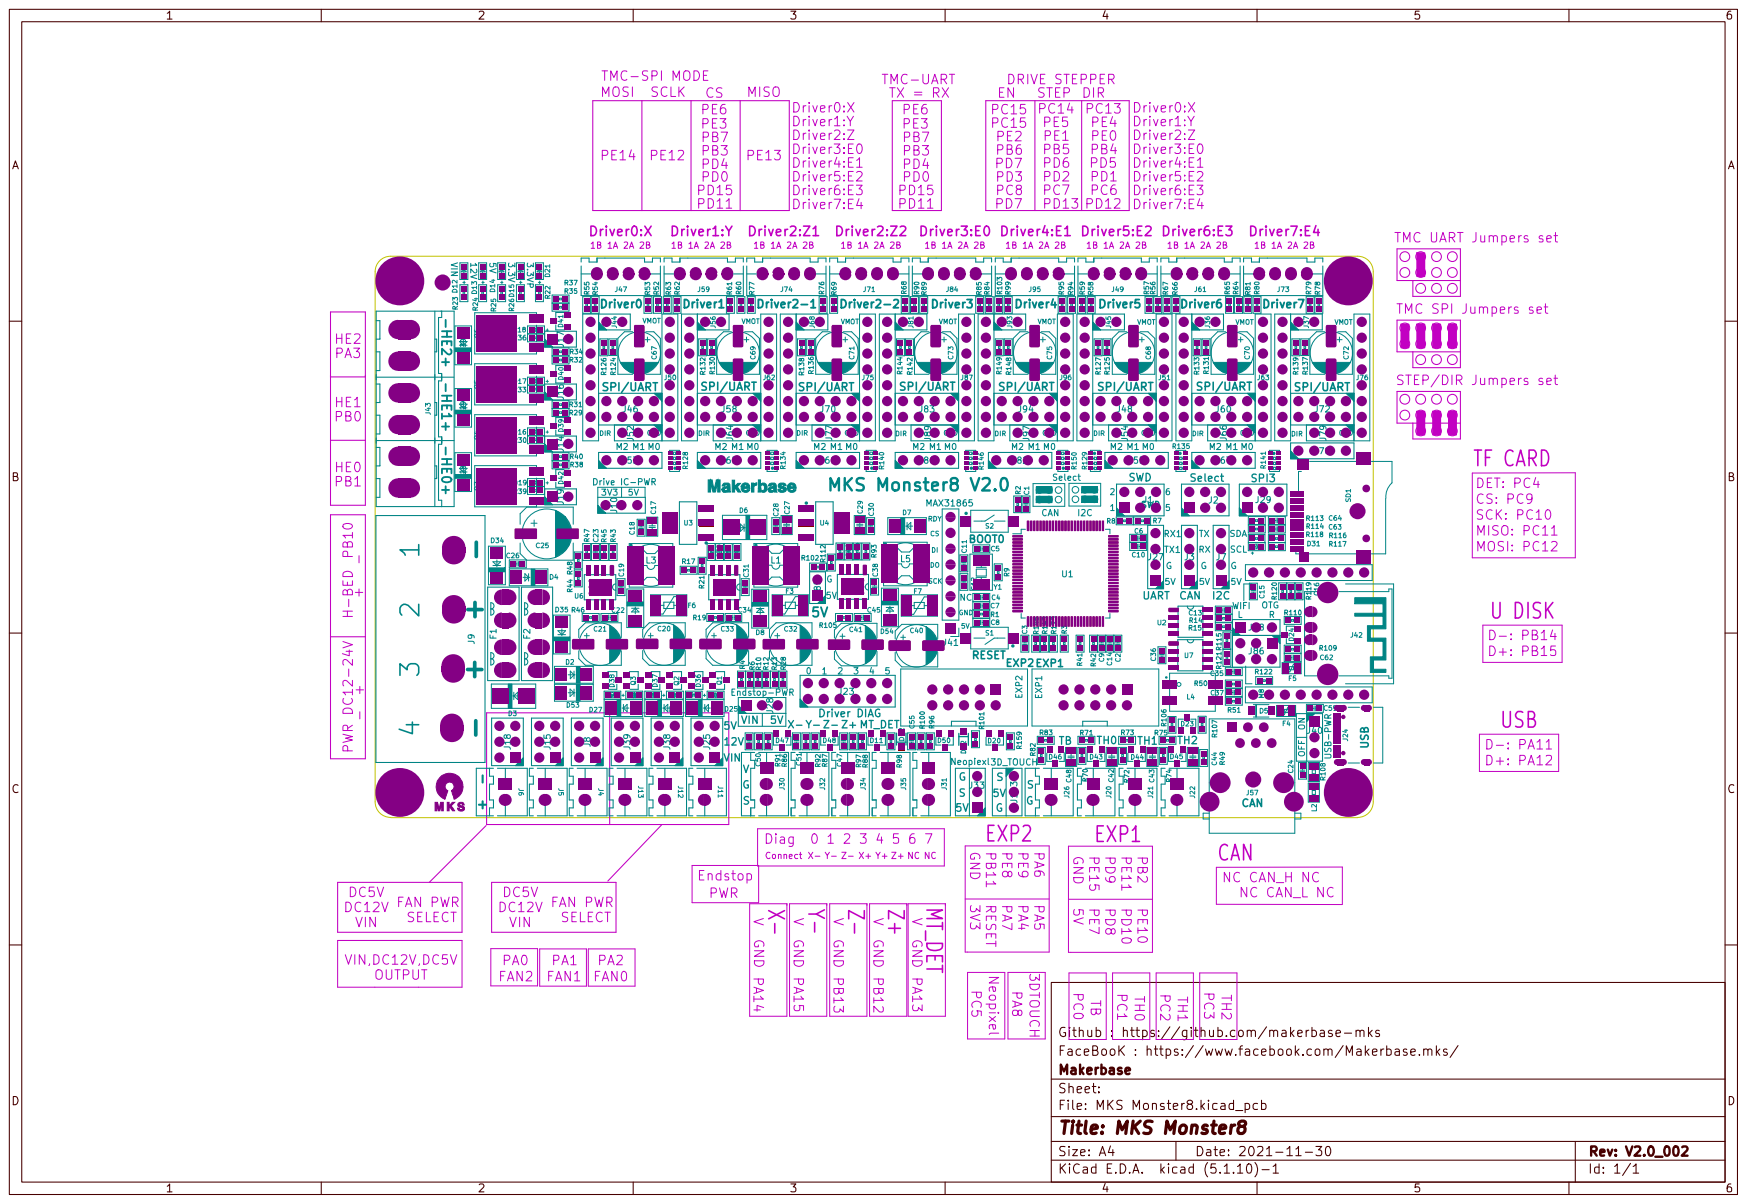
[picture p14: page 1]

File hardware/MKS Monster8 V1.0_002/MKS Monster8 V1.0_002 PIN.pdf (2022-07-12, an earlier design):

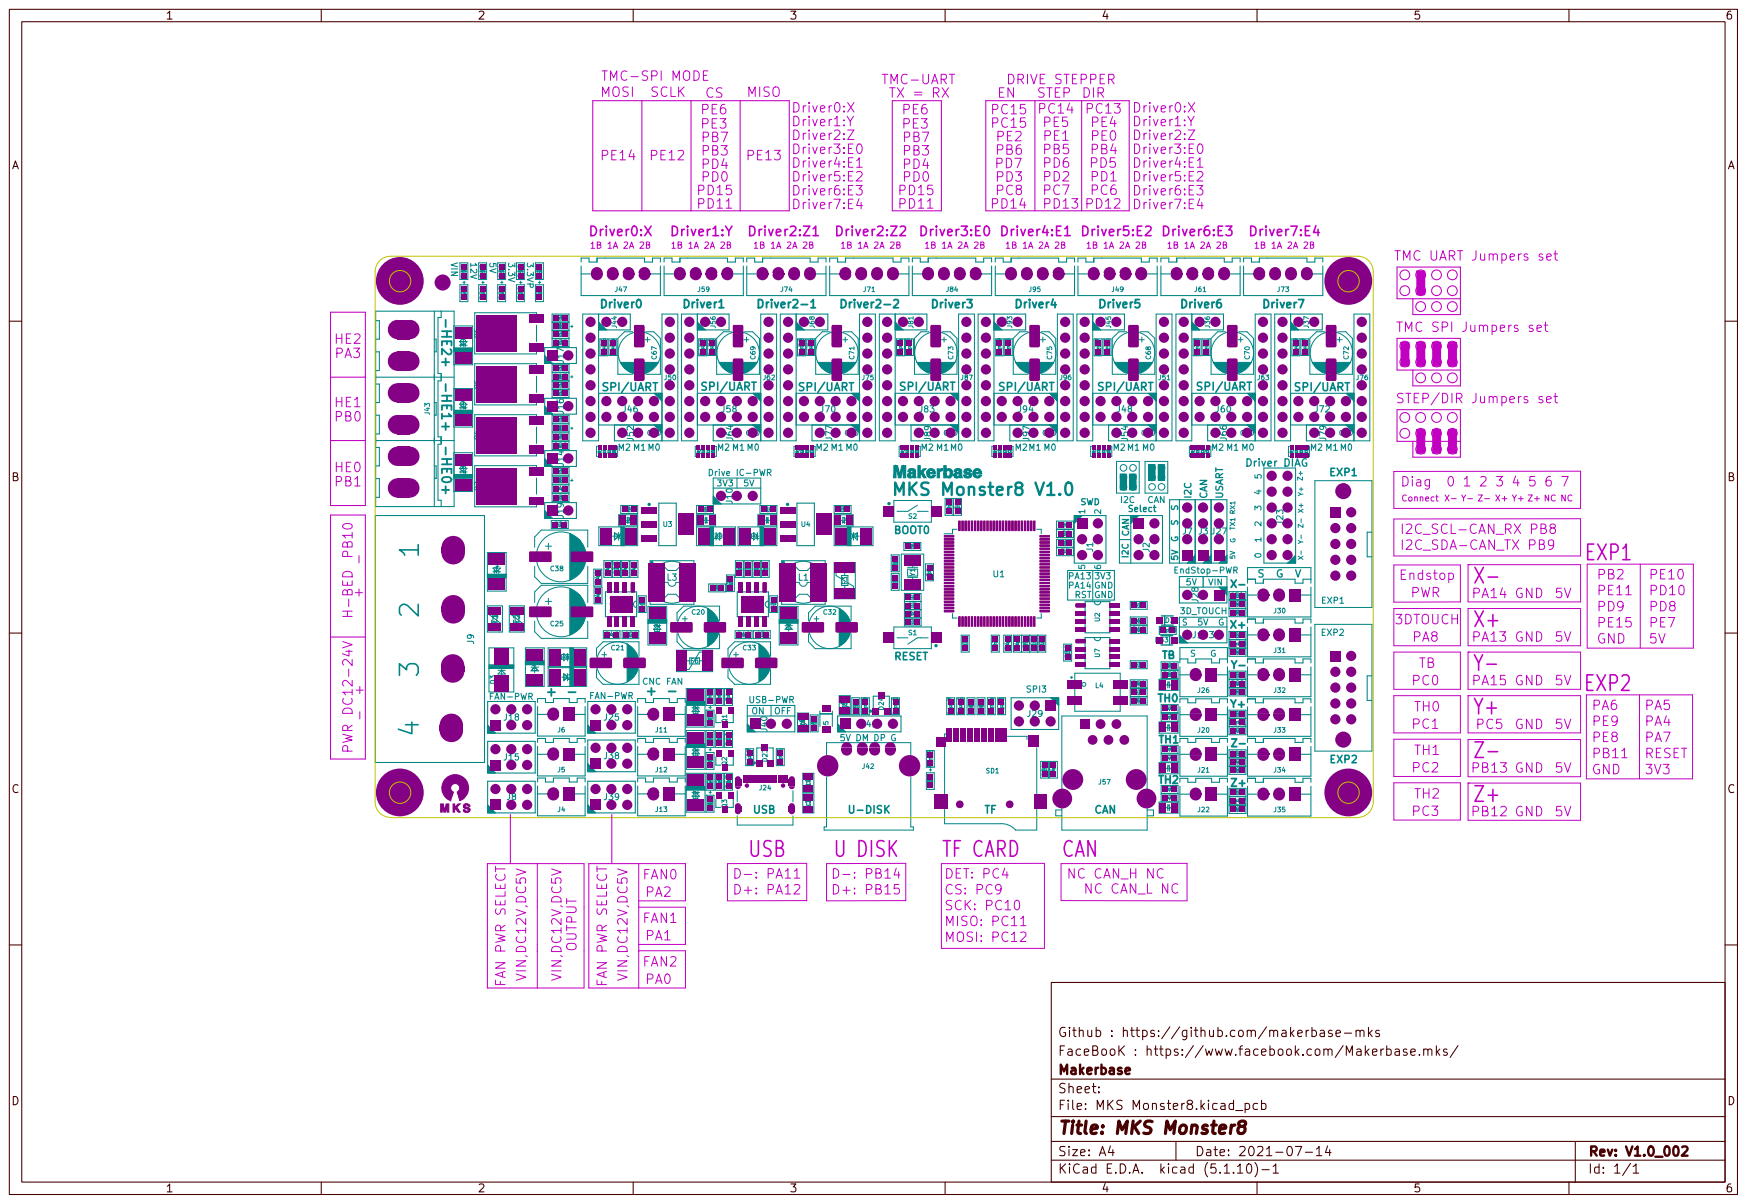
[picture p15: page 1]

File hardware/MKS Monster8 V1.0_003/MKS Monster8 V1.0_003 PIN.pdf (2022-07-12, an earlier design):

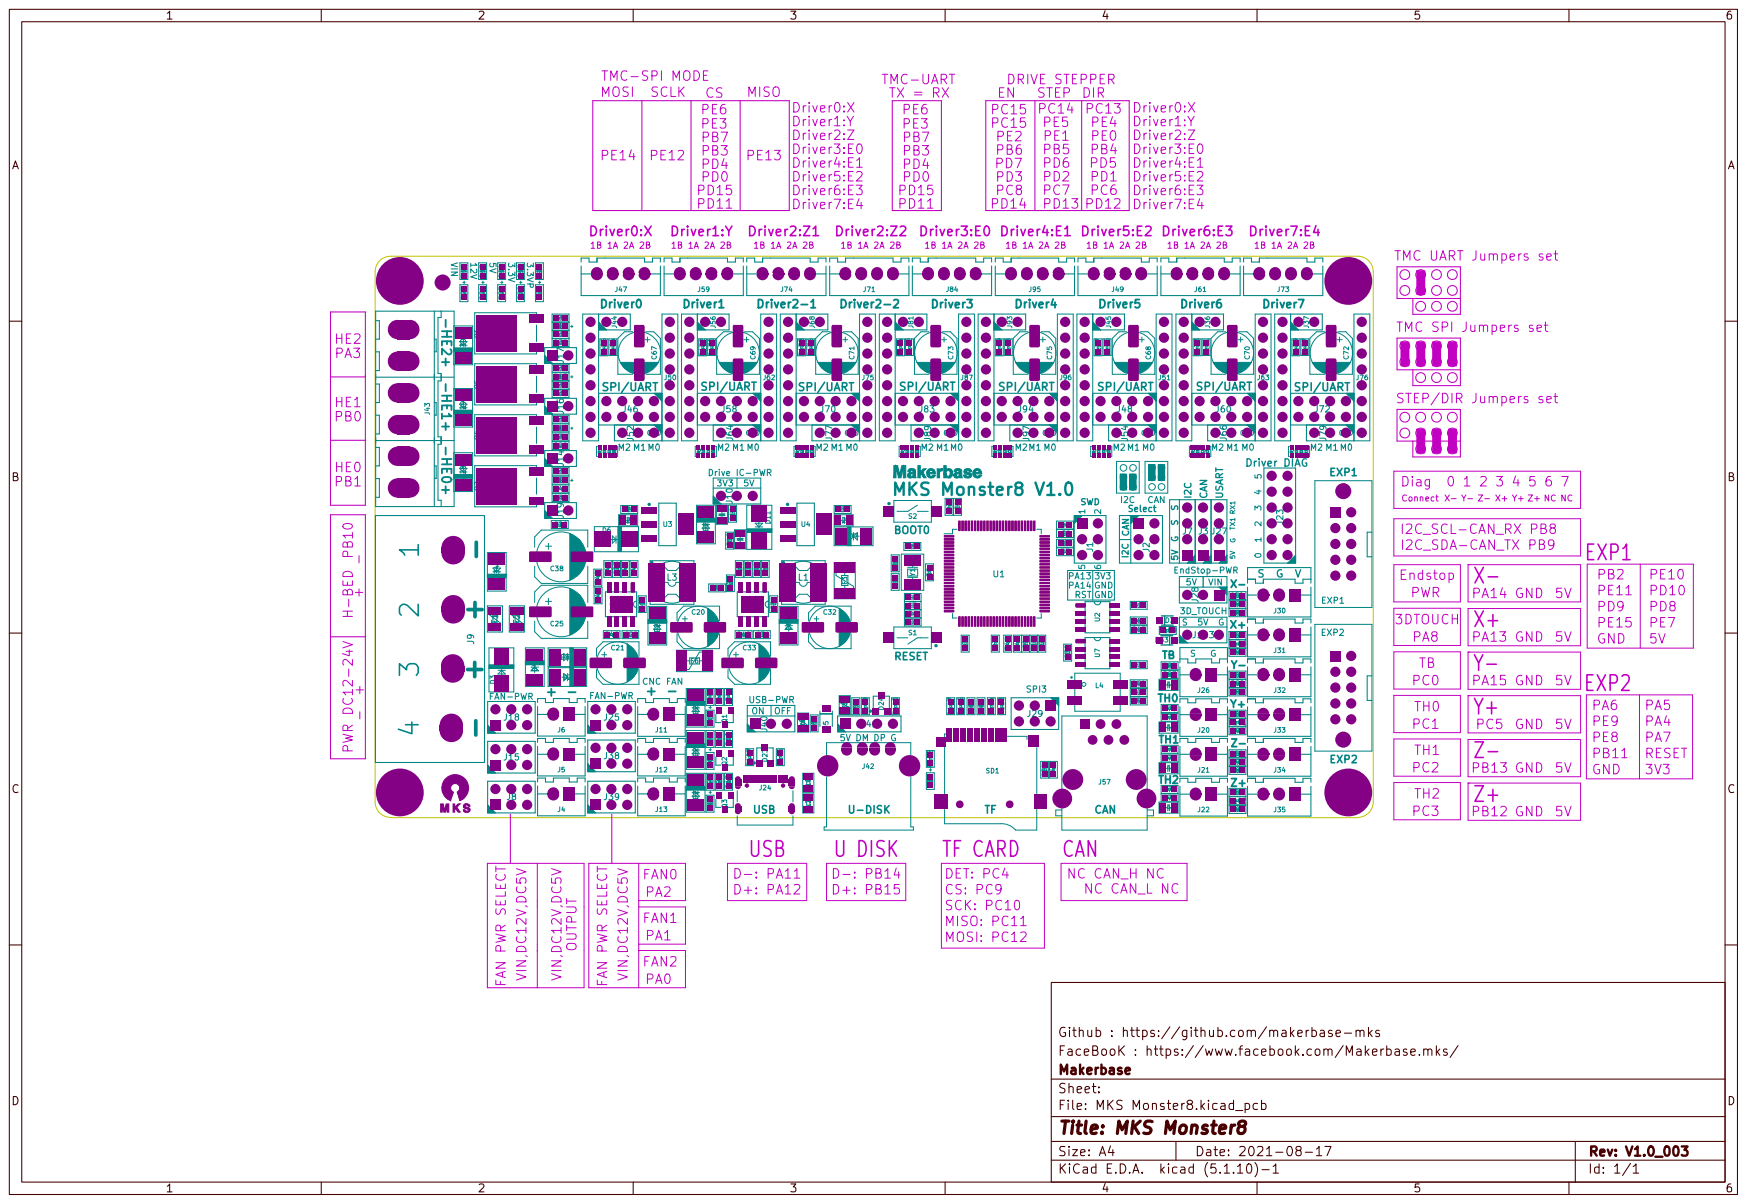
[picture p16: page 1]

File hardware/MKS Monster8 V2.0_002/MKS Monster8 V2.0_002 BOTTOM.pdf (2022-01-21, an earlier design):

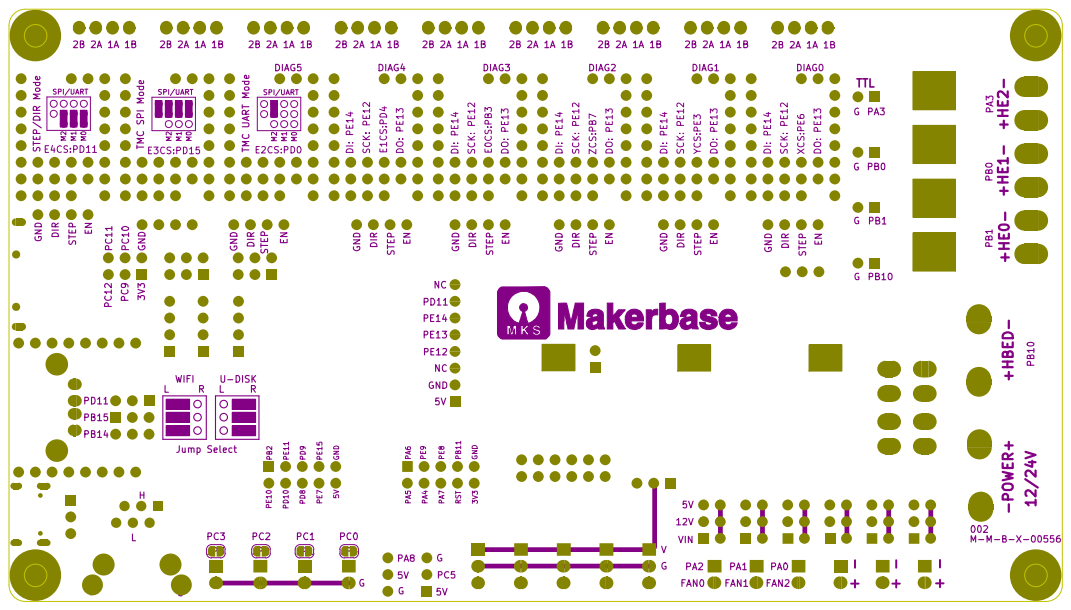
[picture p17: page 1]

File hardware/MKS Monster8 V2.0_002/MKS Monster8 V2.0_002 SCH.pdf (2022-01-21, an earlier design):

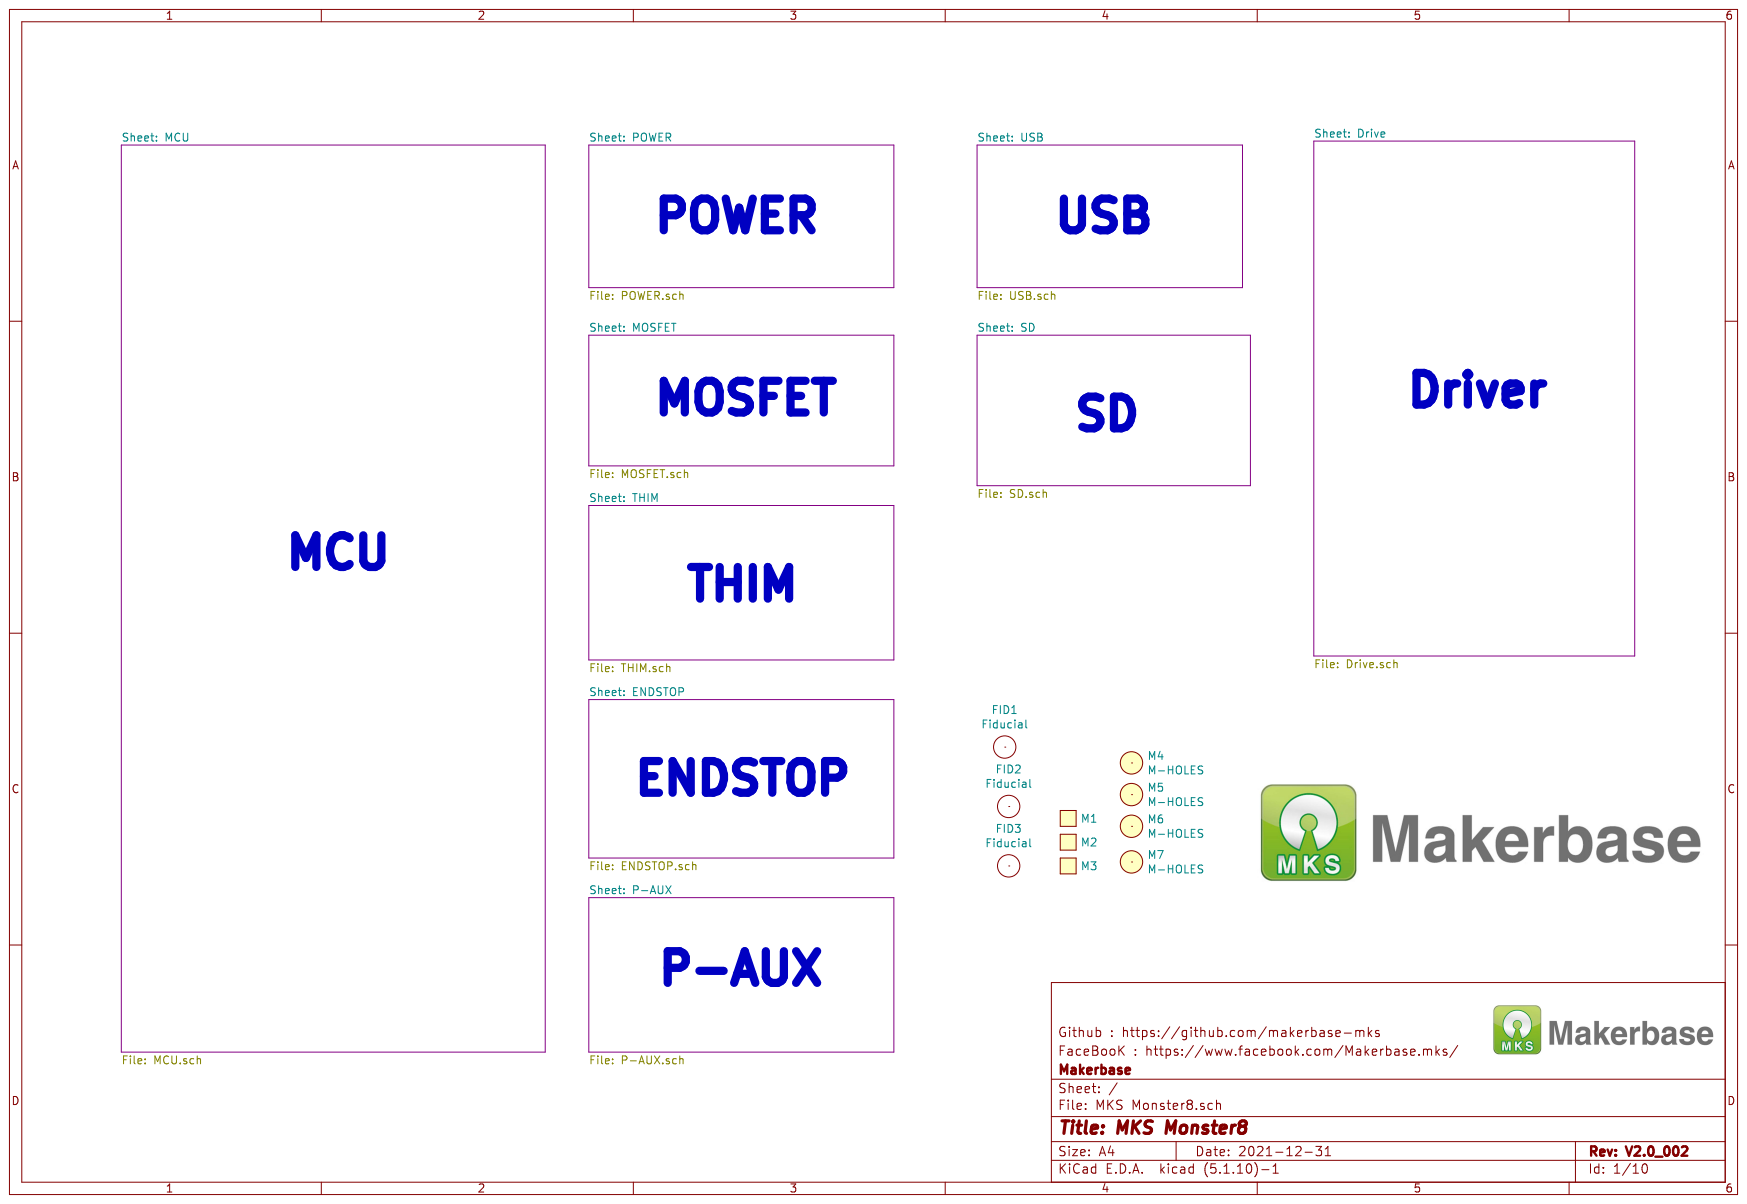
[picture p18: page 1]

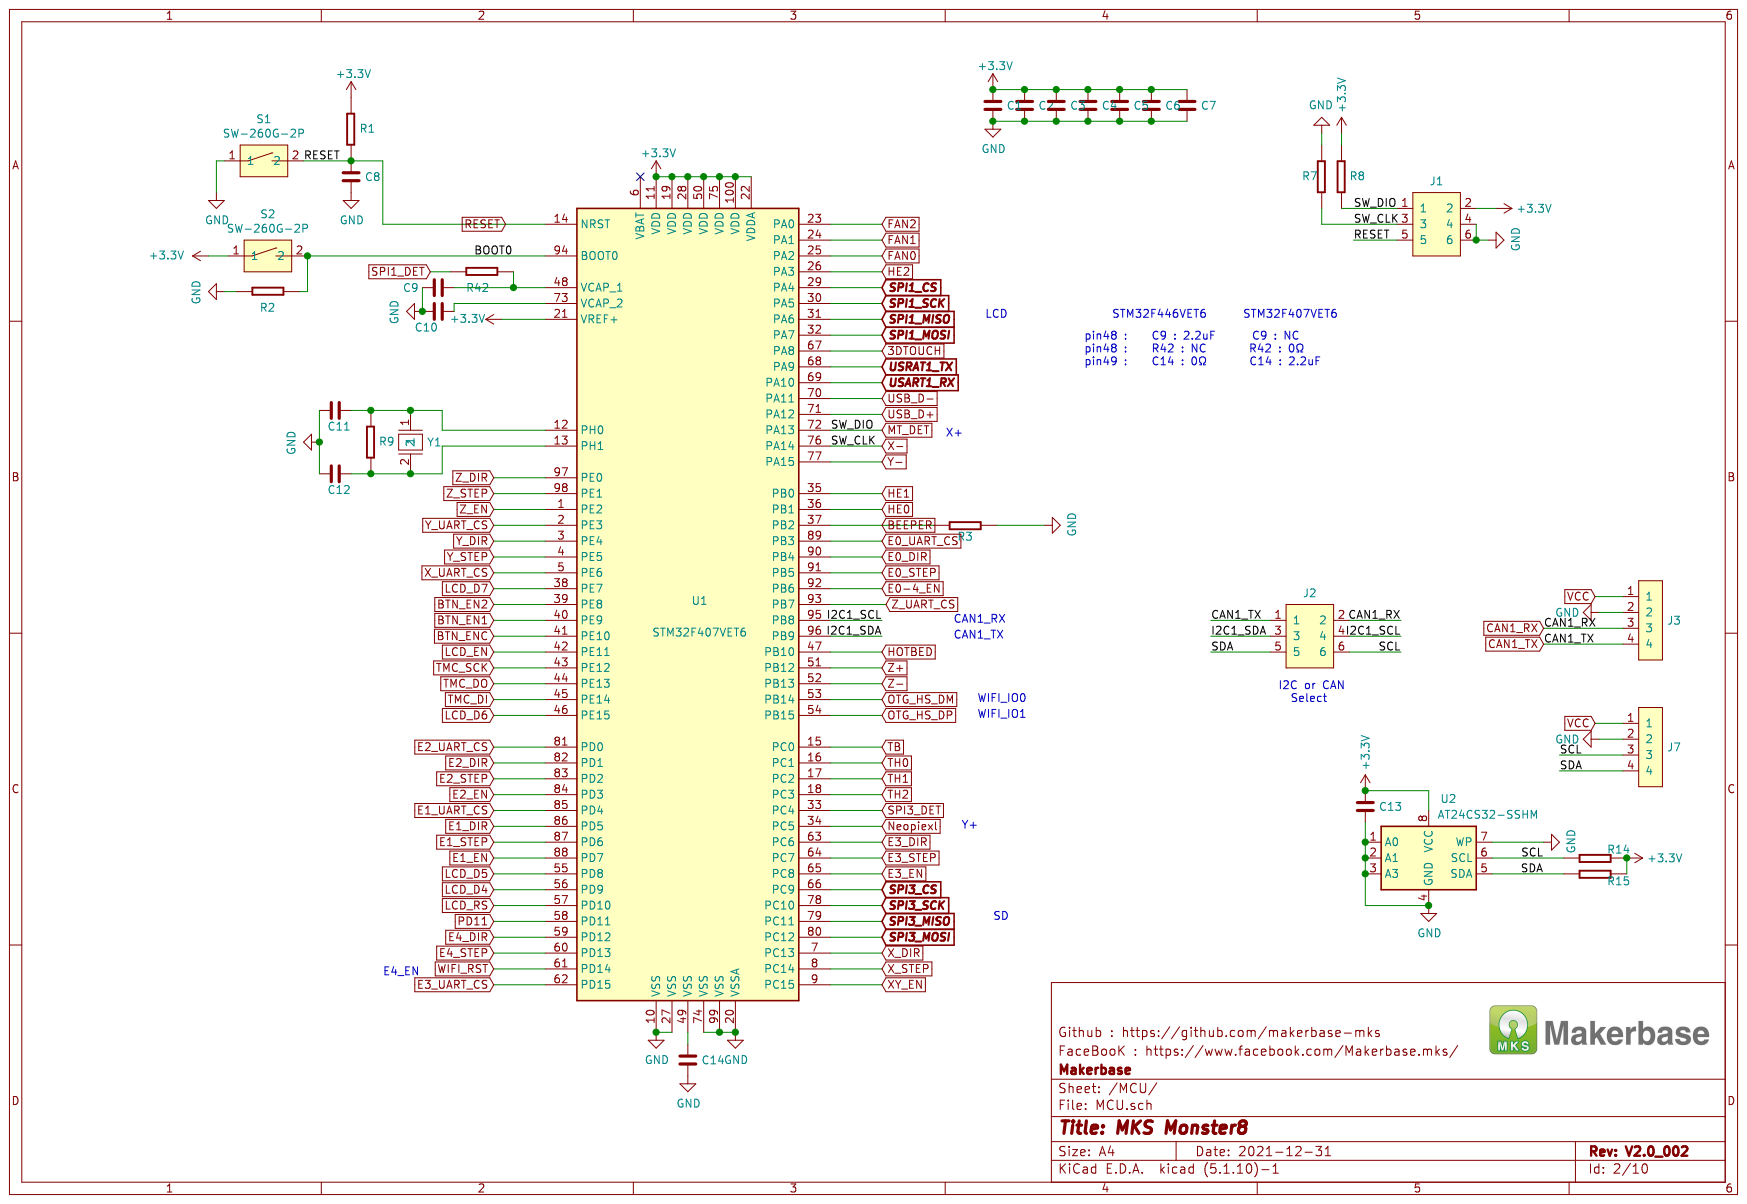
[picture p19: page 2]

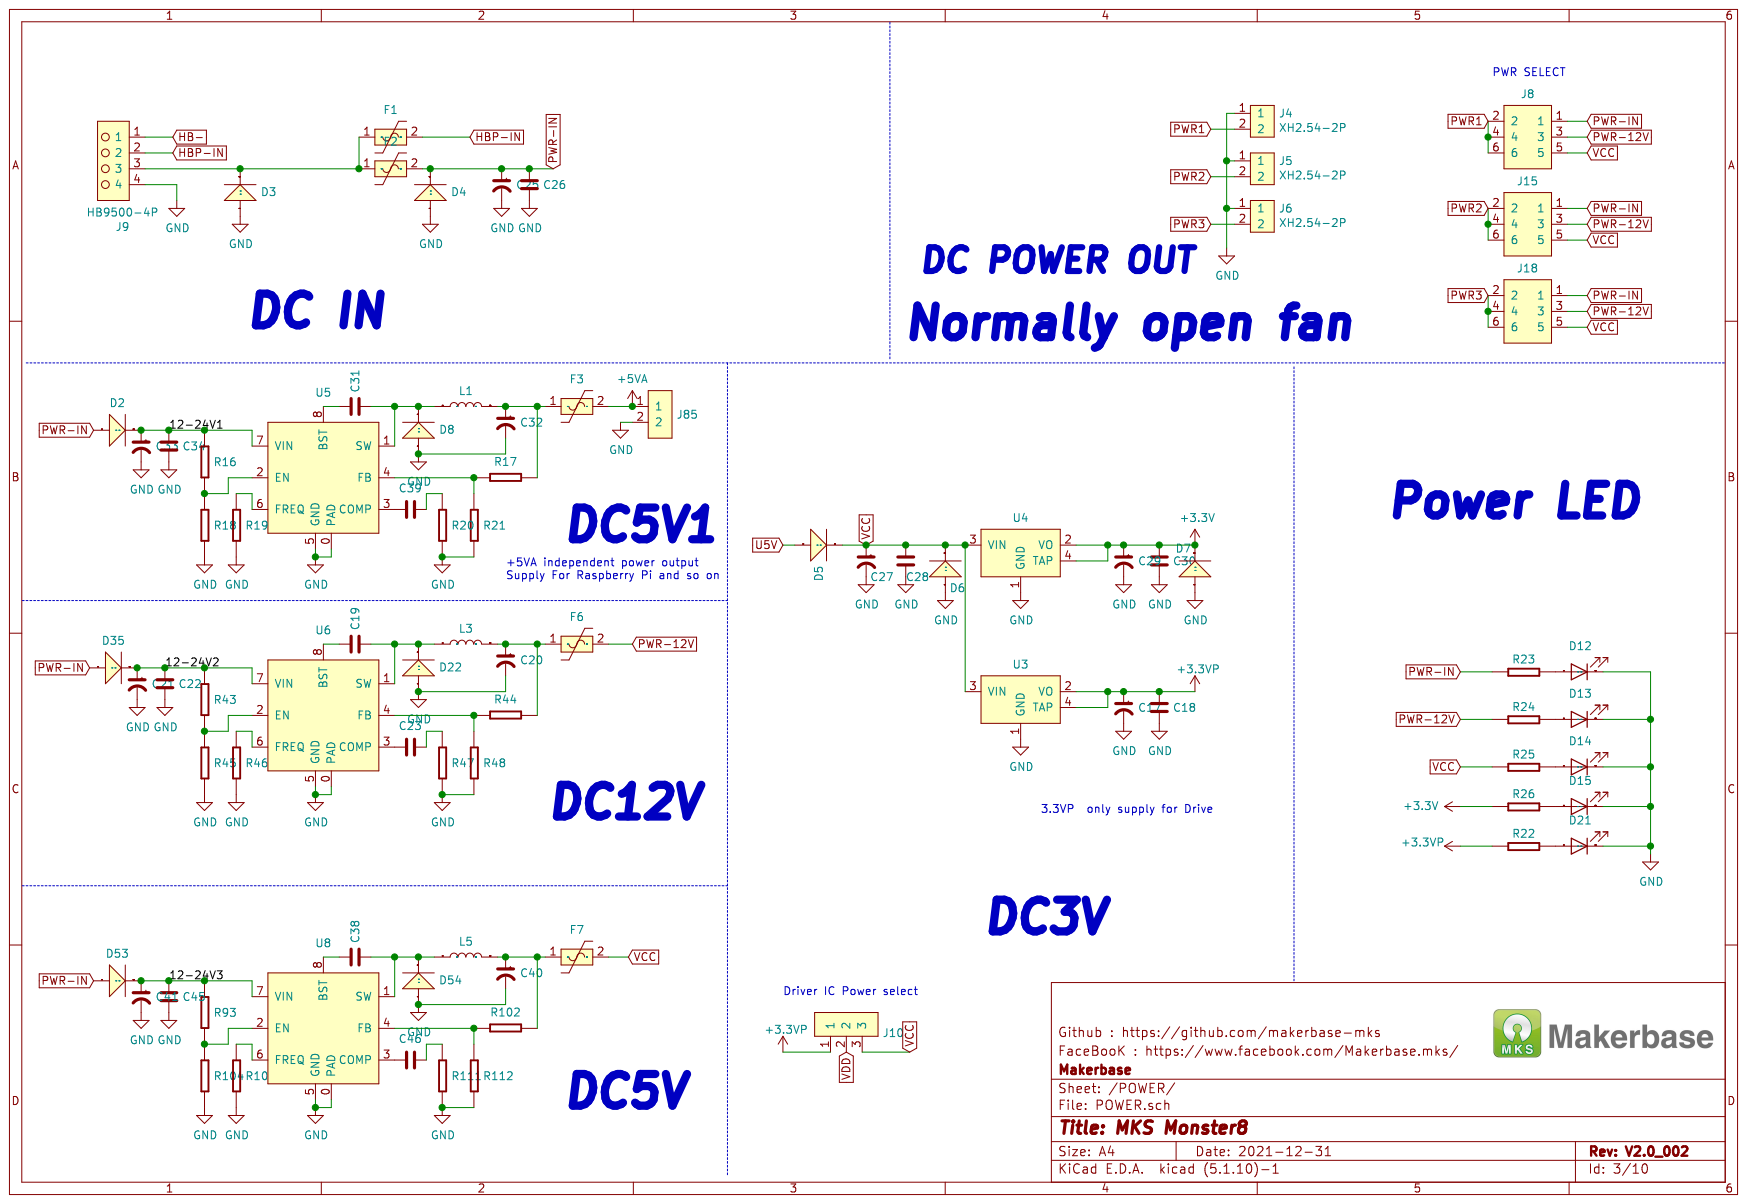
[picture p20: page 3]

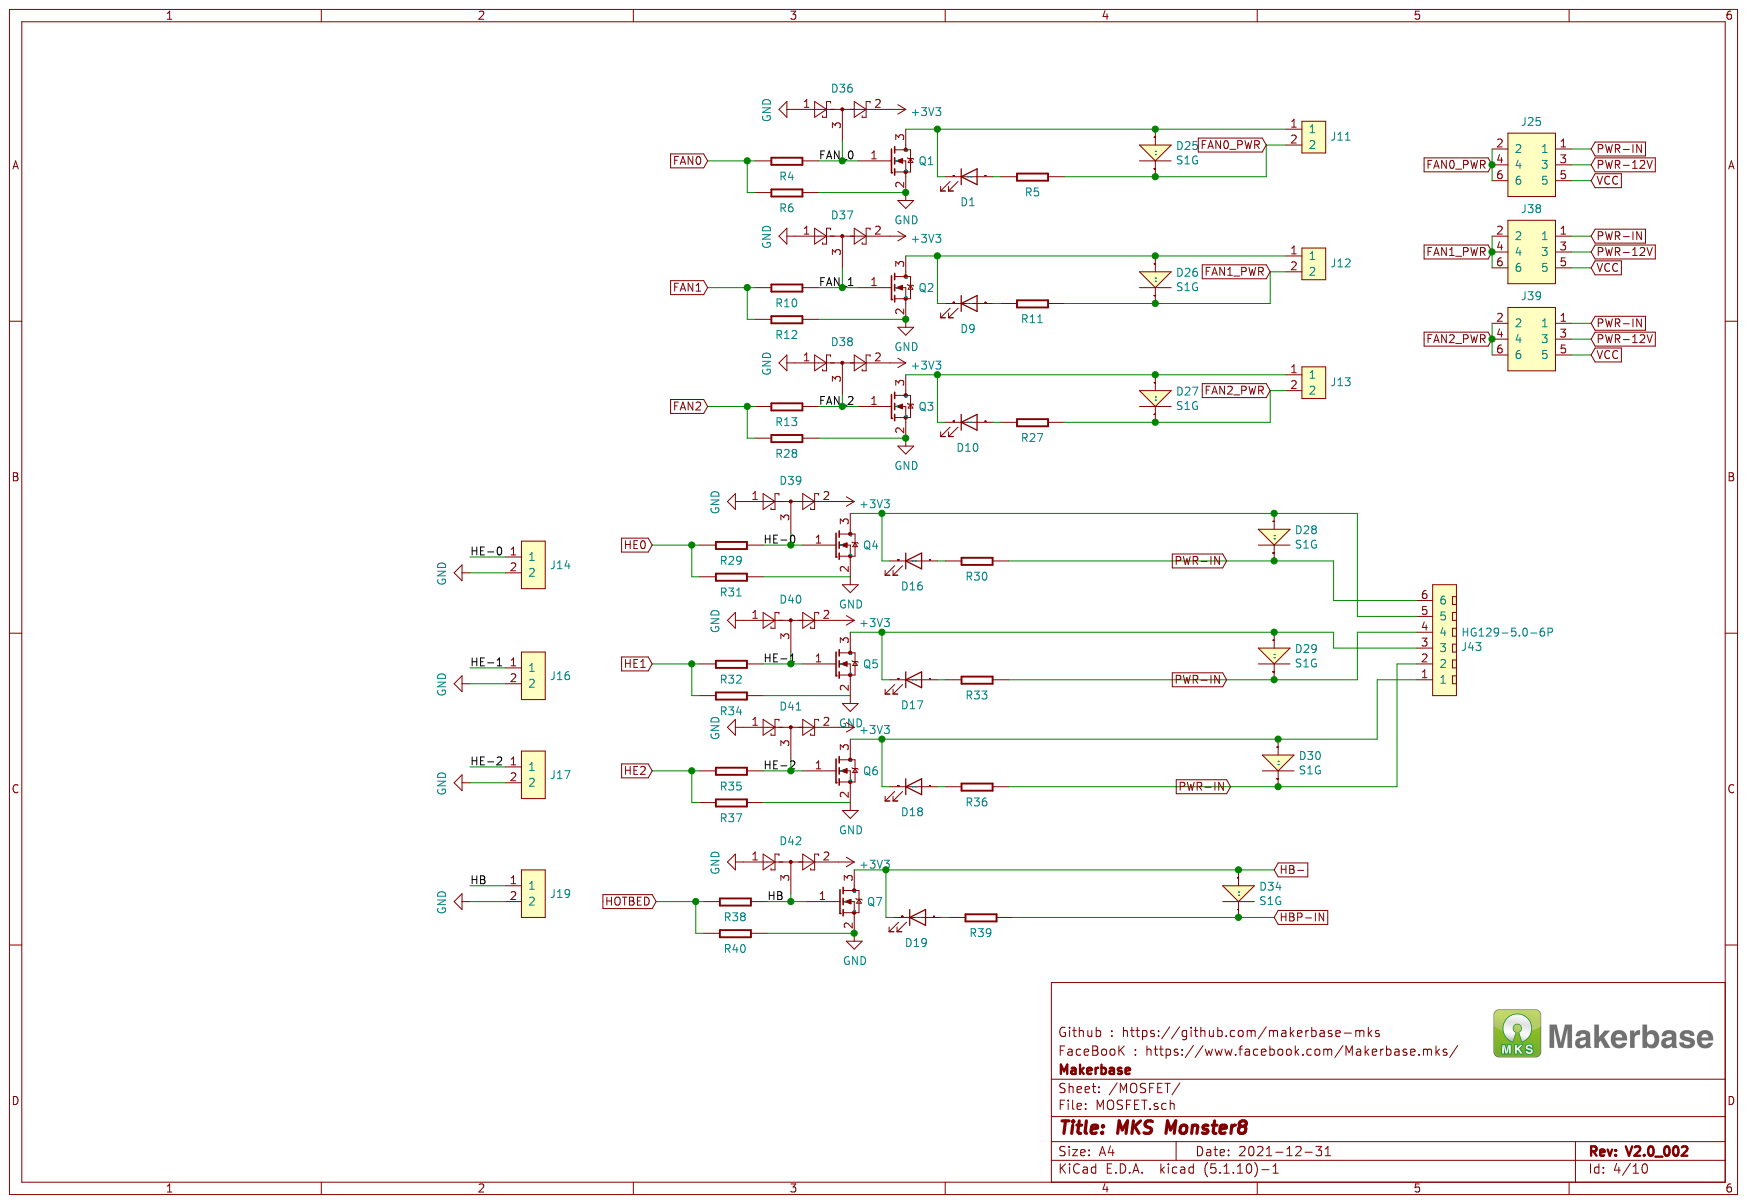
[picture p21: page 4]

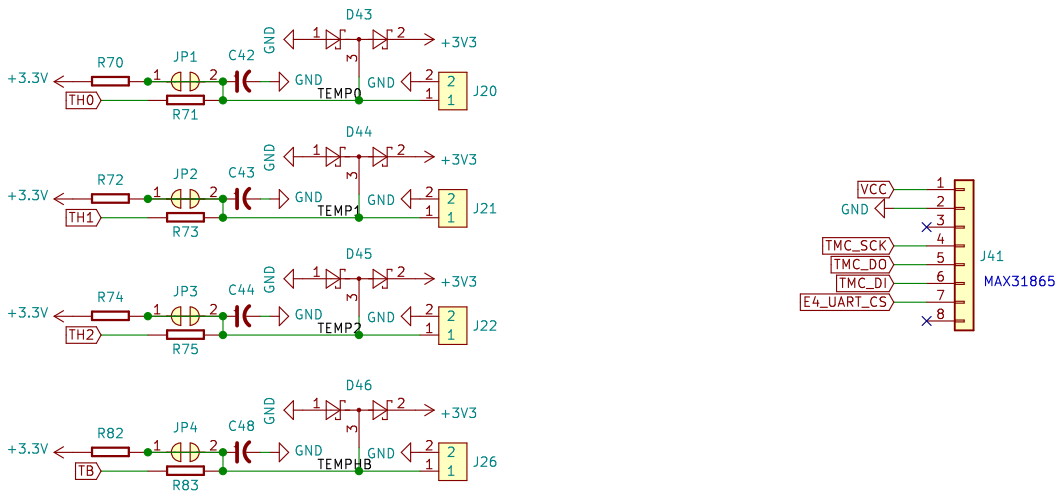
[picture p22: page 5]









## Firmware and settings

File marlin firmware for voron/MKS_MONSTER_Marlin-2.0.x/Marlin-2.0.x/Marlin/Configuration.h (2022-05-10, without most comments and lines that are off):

#pragma once
#define CONFIGURATION_H_VERSION 02000901
#define STRING_CONFIG_H_AUTHOR "(none, default config)" // Who made the changes.
#define SHOW_BOOTSCREEN
#define SERIAL_PORT -1
#define BAUDRATE 250000
#define MOTHERBOARD BOARD_MKS_MONSTER8
#if LINEAR_AXES >= 4
  #define AXIS4_NAME 'A' // :['A', 'B', 'C', 'U', 'V', 'W']
#endif
#if LINEAR_AXES >= 5
  #define AXIS5_NAME 'B' // :['A', 'B', 'C', 'U', 'V', 'W']
#endif
#if LINEAR_AXES >= 6
  #define AXIS6_NAME 'C' // :['A', 'B', 'C', 'U', 'V', 'W']
#endif
#define EXTRUDERS 1
#define DEFAULT_NOMINAL_FILAMENT_DIA 1.75
#define TEMP_SENSOR_0 1
#define TEMP_SENSOR_1 0
#define TEMP_SENSOR_2 0
#define TEMP_SENSOR_3 0
#define TEMP_SENSOR_4 0
#define TEMP_SENSOR_5 0
#define TEMP_SENSOR_6 0
#define TEMP_SENSOR_7 0
#define TEMP_SENSOR_BED 1
#define TEMP_SENSOR_PROBE 0
#define TEMP_SENSOR_CHAMBER 0
#define TEMP_SENSOR_COOLER 0
#define TEMP_SENSOR_REDUNDANT 0
#define DUMMY_THERMISTOR_998_VALUE  25
#define DUMMY_THERMISTOR_999_VALUE 100
#define TEMP_RESIDENCY_TIME         10  // (seconds) Time to wait for hotend to "settle" in M109
#define TEMP_WINDOW                  1  // (°C) Temperature proximity for the "temperature reached" timer
#define TEMP_HYSTERESIS              3  // (°C) Temperature proximity considered "close enough" to the target
#define TEMP_BED_RESIDENCY_TIME     10  // (seconds) Time to wait for bed to "settle" in M190
#define TEMP_BED_WINDOW              1  // (°C) Temperature proximity for the "temperature reached" timer
#define TEMP_BED_HYSTERESIS          3  // (°C) Temperature proximity considered "close enough" to the target
#define TEMP_CHAMBER_RESIDENCY_TIME 10  // (seconds) Time to wait for chamber to "settle" in M191
#define TEMP_CHAMBER_WINDOW          1  // (°C) Temperature proximity for the "temperature reached" timer
#define TEMP_CHAMBER_HYSTERESIS      3  // (°C) Temperature proximity considered "close enough" to the target
#if TEMP_SENSOR_REDUNDANT
  #define TEMP_SENSOR_REDUNDANT_SOURCE     1  // The sensor that will provide the redundant reading.
  #define TEMP_SENSOR_REDUNDANT_TARGET     0  // The sensor that we are providing a redundant reading for.
  #define TEMP_SENSOR_REDUNDANT_MAX_DIFF  10  // (°C) Temperature difference that will trigger a print abort.
#endif
#define HEATER_0_MINTEMP   5
#define HEATER_1_MINTEMP   5
#define HEATER_2_MINTEMP   5
#define HEATER_3_MINTEMP   5
#define HEATER_4_MINTEMP   5
#define HEATER_5_MINTEMP   5
#define HEATER_6_MINTEMP   5
#define HEATER_7_MINTEMP   5
#define BED_MINTEMP        5
#define CHAMBER_MINTEMP    5
#define HEATER_0_MAXTEMP 275
#define HEATER_1_MAXTEMP 275
#define HEATER_2_MAXTEMP 275
#define HEATER_3_MAXTEMP 275
#define HEATER_4_MAXTEMP 275
#define HEATER_5_MAXTEMP 275
#define HEATER_6_MAXTEMP 275
#define HEATER_7_MAXTEMP 275
#define BED_MAXTEMP      150
#define CHAMBER_MAXTEMP  60
#define HOTEND_OVERSHOOT 15   // (°C) Forbid temperatures over MAXTEMP - OVERSHOOT
#define BED_OVERSHOOT    10   // (°C) Forbid temperatures over MAXTEMP - OVERSHOOT
#define COOLER_OVERSHOOT  2   // (°C) Forbid temperatures closer than OVERSHOOT
#define PIDTEMP
#define BANG_MAX 255     // Limits current to nozzle while in bang-bang mode; 255=full current
#define PID_MAX BANG_MAX // Limits current to nozzle while PID is active (see PID_FUNCTIONAL_RANGE below); 255=full current
#define PID_K1 0.95      // Smoothing factor within any PID loop
    #define DEFAULT_Kp  22.20
    #define DEFAULT_Ki   1.08
    #define DEFAULT_Kd 114.00
#define MAX_BED_POWER 255 // limits duty cycle to bed; 255=full current
#define MAX_CHAMBER_POWER 255 // limits duty cycle to chamber heater; 255=full current
  #define PID_FUNCTIONAL_RANGE 10 // If the temperature difference between the target temperature and the actual temperature
#define PREVENT_COLD_EXTRUSION
#define EXTRUDE_MINTEMP 170
#define PREVENT_LENGTHY_EXTRUDE
#define EXTRUDE_MAXLENGTH 200
#define THERMAL_PROTECTION_HOTENDS // Enable thermal protection for all extruders
#define THERMAL_PROTECTION_BED     // Enable thermal protection for the heated bed
#define THERMAL_PROTECTION_CHAMBER // Enable thermal protection for the heated chamber
#define THERMAL_PROTECTION_COOLER  // Enable thermal protection for the laser cooling
#define COREXY
#define USE_ZMIN_PLUG
#define USE_XMAX_PLUG
#define USE_YMAX_PLUG
#define ENDSTOPPULLUPS
#define X_MIN_ENDSTOP_INVERTING false // Set to true to invert the logic of the endstop.
#define Y_MIN_ENDSTOP_INVERTING false // Set to true to invert the logic of the endstop.
#define Z_MIN_ENDSTOP_INVERTING true// Set to true to invert the logic of the endstop.
#define I_MIN_ENDSTOP_INVERTING false // Set to true to invert the logic of the endstop.
#define J_MIN_ENDSTOP_INVERTING false // Set to true to invert the logic of the endstop.
#define K_MIN_ENDSTOP_INVERTING false // Set to true to invert the logic of the endstop.
#define X_MAX_ENDSTOP_INVERTING false // Set to true to invert the logic of the endstop.
#define Y_MAX_ENDSTOP_INVERTING false // Set to true to invert the logic of the endstop.
#define Z_MAX_ENDSTOP_INVERTING false // Set to true to invert the logic of the endstop.
#define I_MAX_ENDSTOP_INVERTING false // Set to true to invert the logic of the endstop.
#define J_MAX_ENDSTOP_INVERTING false // Set to true to invert the logic of the endstop.
#define K_MAX_ENDSTOP_INVERTING false // Set to true to invert the logic of the endstop.
#define Z_MIN_PROBE_ENDSTOP_INVERTING true // Set to true to invert the logic of the probe.
#define X_DRIVER_TYPE  TMC2209
#define Y_DRIVER_TYPE  TMC2209
#define Z_DRIVER_TYPE  TMC2209
#define Z2_DRIVER_TYPE TMC2209
#define Z3_DRIVER_TYPE TMC2209
#define Z4_DRIVER_TYPE TMC2209
#define E0_DRIVER_TYPE TMC2209
#define DEFAULT_AXIS_STEPS_PER_UNIT   { 80, 80, 400, 382.1666 }
#define DEFAULT_MAX_FEEDRATE          { 300, 300, 5, 25 }
#define DEFAULT_MAX_ACCELERATION      { 2500, 2500, 100, 5000 }
#define DEFAULT_ACCELERATION          3000    // X, Y, Z and E acceleration for printing moves
#define DEFAULT_RETRACT_ACCELERATION  3000    // E acceleration for retracts
#define DEFAULT_TRAVEL_ACCELERATION   3000    // X, Y, Z acceleration for travel (non printing) moves
 #define CLASSIC_JERK
  #define DEFAULT_XJERK 10.0
  #define DEFAULT_YJERK 10.0
  #define DEFAULT_ZJERK  0.3
#define DEFAULT_EJERK    5.0  // May be used by Linear Advance
#define Z_MIN_PROBE_USES_Z_MIN_ENDSTOP_PIN
#define FIX_MOUNTED_PROBE
#define NOZZLE_TO_PROBE_OFFSET { 0, 25, -3.7}
#define PROBING_MARGIN 10
#define XY_PROBE_FEEDRATE (133*60)
#define Z_PROBE_FEEDRATE_FAST (4*60)
#define Z_PROBE_FEEDRATE_SLOW (Z_PROBE_FEEDRATE_FAST / 2)
#define Z_CLEARANCE_DEPLOY_PROBE   10 // Z Clearance for Deploy/Stow
#define Z_CLEARANCE_BETWEEN_PROBES  5 // Z Clearance between probe points
#define Z_CLEARANCE_MULTI_PROBE     5 // Z Clearance between multiple probes
#define Z_PROBE_LOW_POINT          -4 // Farthest distance below the trigger-point to go before stopping
#define Z_PROBE_OFFSET_RANGE_MIN -20
#define Z_PROBE_OFFSET_RANGE_MAX 20
#define X_ENABLE_ON 0
#define Y_ENABLE_ON 0
#define Z_ENABLE_ON 0
#define E_ENABLE_ON 0 // For all extruders
#define DISABLE_X false
#define DISABLE_Y false
#define DISABLE_Z false
#define DISABLE_E false             // Disable the extruder when not stepping
#define DISABLE_INACTIVE_EXTRUDER   // Keep only the active extruder enabled
#define INVERT_X_DIR true
#define INVERT_Y_DIR true
#define INVERT_Z_DIR true
#define INVERT_E0_DIR true
#define INVERT_E1_DIR false
#define INVERT_E2_DIR false
#define INVERT_E3_DIR false
#define INVERT_E4_DIR false
#define INVERT_E5_DIR false
#define INVERT_E6_DIR false
#define INVERT_E7_DIR false
#define X_HOME_DIR 1
#define Y_HOME_DIR 1
#define Z_HOME_DIR -1
#define X_BED_SIZE 230
#define Y_BED_SIZE 230
#define X_MIN_POS 0
#define Y_MIN_POS 0
#define Z_MIN_POS 0
#define X_MAX_POS X_BED_SIZE
#define Y_MAX_POS Y_BED_SIZE
#define Z_MAX_POS 230
#define MIN_SOFTWARE_ENDSTOPS
  #define MIN_SOFTWARE_ENDSTOP_X
  #define MIN_SOFTWARE_ENDSTOP_Y
  #define MIN_SOFTWARE_ENDSTOP_Z
  #define MIN_SOFTWARE_ENDSTOP_I
  #define MIN_SOFTWARE_ENDSTOP_J
  #define MIN_SOFTWARE_ENDSTOP_K
#define MAX_SOFTWARE_ENDSTOPS
  #define MAX_SOFTWARE_ENDSTOP_X
  #define MAX_SOFTWARE_ENDSTOP_Y
  #define MAX_SOFTWARE_ENDSTOP_Z
  #define MAX_SOFTWARE_ENDSTOP_I
  #define MAX_SOFTWARE_ENDSTOP_J
  #define MAX_SOFTWARE_ENDSTOP_K
 #define Z_SAFE_HOMING
  #define Z_SAFE_HOMING_X_POINT X_CENTER  // X point for Z homing
  #define Z_SAFE_HOMING_Y_POINT Y_CENTER  // Y point for Z homing
#define HOMING_FEEDRATE_MM_M { (50*60), (50*60), (4*60) }
#define VALIDATE_HOMING_ENDSTOPS
#define EEPROM_SETTINGS     // Persistent storage with M500 and M501
#define EEPROM_CHITCHAT       // Give feedback on EEPROM commands. Disable to save PROGMEM.
  #define EEPROM_AUTO_INIT  // Init EEPROM automatically on any errors.
#define HOST_KEEPALIVE_FEATURE        // Disable this if your host doesn't like keepalive messages
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

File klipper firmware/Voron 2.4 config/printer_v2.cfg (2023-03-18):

# See docs/Config_Reference.md for a description of parameters.

[mcu]
## Obtain definition by "ls -l /dev/serial/by-id/" then unplug to verify
serial: /dev/serial/by-id/usb-Klipper_stm32f407xx_53004C001250424B32333720-if00


#--------------------------------------------------------------------
##--------------------------------------------------------------------
[printer]
kinematics: corexy
max_velocity: 150  
max_accel: 2000   			#Max 4000
max_z_velocity: 15 			#Max 15 for 12V TMC Drivers, can increase for 24V
max_z_accel: 30
square_corner_velocity: 5.0

[stepper_x]
step_pin:PC14
dir_pin:!PC13
enable_pin:!PC15
microsteps: 16
rotation_distance: 40
full_steps_per_rotation:200  #set to 400 for 0.9 degree stepper
endstop_pin:PA14
position_min: 0  
position_endstop: 230
position_max: 230

#--------------------------------------------------------------------
homing_speed:50
homing_retract_dist:5
homing_positive_dir:true

[stepper_y]
step_pin:PE5
dir_pin:!PE4
enable_pin:!PC15
microsteps:16
rotation_distance: 40
full_steps_per_rotation:200  #set to 400 for 0.9 degree stepper
endstop_pin:PA15
position_min: 0
position_endstop:230
position_max:230

#--------------------------------------------------------------------
homing_speed:50
homing_retract_dist:5
homing_positive_dir:true

[stepper_z]
step_pin:PE1
dir_pin:!PE0
enable_pin: !PE2
microsteps: 16
rotation_distance: 40
full_steps_per_rotation: 200
gear_ratio: 80:16
endstop_pin:probe:z_virtual_endstop ## PB12 for Z-max; endstop have'!' is NO

##  Z-position of nozzle (in mm) to z-endstop trigger point relative to print surface (Z0)
##  (+) value = endstop above Z0, (-) value = endstop below
##	Increasing position_endstop brings nozzle closer to the bed
##  After you run Z_ENDSTOP_CALIBRATE, position_endstop will be stored at the very end of your config
#position_endstop:-5
position_max: 230
position_min: -15 
homing_speed: 8
second_homing_speed: 3

[stepper_z1]
step_pin:PD6
dir_pin:PD5
enable_pin:!PD7
microsteps:16
rotation_distance: 40
full_steps_per_rotation: 200
gear_ratio: 80:16

[stepper_z2]
step_pin:PD2
dir_pin:PD1
enable_pin:!PD3
microsteps: 16
rotation_distance: 40
full_steps_per_rotation: 200
gear_ratio: 80:16

[stepper_z3]
step_pin:PC7
dir_pin:PC6
enable_pin:!PC8
microsteps:16
rotation_distance:40
full_steps_per_rotation: 200
gear_ratio:80:16


[extruder]
step_pin:PB5
dir_pin:!PB4
enable_pin:!PB6
microsteps:16
rotation_distance: 25.12	#Bondtech 5mm Drive Gears
gear_ratio: 50:17
full_steps_per_rotation: 200	#200 for 1.8 degree, 400 for 0.9 degree
nozzle_diameter: 0.400
filament_diameter: 1.750
min_temp: 0
max_temp: 275
heater_pin: PB1
sensor_type:  NTC 100K MGB18-104F39050L32
sensor_pin: PC1
max_power: 1.0
control : pid  
pid_kp : 26.213 
pid_ki : 1.304
pid_kd : 131.721 
pressure_advance: 0.05 
pressure_advance_smooth_time: 0.040

#[extruder1]
#step_pin: PD6
#dir_pin: !PD5
#enable_pin: !PD7
#heater_pin: PB0
#sensor_pin: PC2

#[extruder2]
#step_pin: PD2
#dir_pin: !PD1
#enable_pin: !PD3
#heater_pin: PA3
#sensor_pin: PC3

#[extruder3]
#step_pin: PC7
#dir_pin: PC6
#enable_pin: !PC8

#[extruder4]
#step_pin: PD13
#dir_pin: !PD12
#enable_pin: !PD14

[heater_bed]
heater_pin: PB10
sensor_type: NTC 100K MGB18-104F39050L32
sensor_pin: PC0
max_power: 1.0
control = pid
pid_kp = 71.039
pid_ki = 2.223
pid_kd = 567.421
min_temp: 0
max_temp: 200

#fan for printed model FAN0
[fan]
pin: PA2

#fan for hotend FAN1
#[heater_fan my_nozzle_fan]
[heater_fan fan1]
pin: PA1
shutdown_speed: 1

#fan for control board FAN2
#[heater_fan my_control_fan]
[heater_fan fan2]
pin: PA0
shutdown_speed: 1

#####################################################################
#	Homing and Gantry Adjustment Routines
#####################################################################
[idle_timeout]
timeout: 3600

[safe_z_home]
home_xy_position: 125,125 # Change coordinates to the center of your print bed
speed: 100
z_hop: 10                 # Move up 10mm
z_hop_speed: 5

[quad_gantry_level]
gantry_corners:
	-58,-7
    308,318
##	Probe points
points:
	30,30
	30,180
	180,180
	180,30
speed: 80
horizontal_move_z: 10
retries: 1
retry_tolerance: 0.05
max_adjust: 30

#####################################################################
# 	Probe
#####################################################################
[probe]
pin:!PB12
x_offset: 0
y_offset: 25.0
z_offset: 3.6
speed: 10.0
samples: 2
samples_result: median
sample_retract_dist: 3.0
samples_tolerance: 0.05
samples_tolerance_retries: 1

#####################################################################
# LED Control
#####################################################################

#[output_pin caselight ](Use PA9)
##  Chamber Lighting - In 5V-RGB Position
#pin: PA9
#pwm: true
#shutdown_value: 0
#value:100
#cycle_time: 0.01

########################################
# TMC UART configuration
########################################

[tmc2209 stepper_x]
uart_pin: PE6
interpolate: True
run_current: 0.8
hold_current: 0.3
sense_resistor: 0.110
stealthchop_threshold: 9999

[tmc2209 stepper_y]
uart_pin: PE3
interpolate: True
run_current: 0.8
hold_current: 0.3
sense_resistor: 0.110
stealthchop_threshold: 9999

[tmc2209 stepper_z]
uart_pin: PB7
interpolate: True
run_current: 0.8
hold_current: 0.5
stealthchop_threshold: 0

[tmc2209 extruder]
uart_pin: PB3
interpolate: True
run_current: 0.6
hold_current: 0.5
sense_resistor: 0.110
stealthchop_threshold: 9999

[tmc2209 stepper_z1]
uart_pin: PD4
interpolate: True
run_current: 0.8
hold_current: 0.5
stealthchop_threshold: 0

[tmc2209 stepper_z2]
uart_pin: PD0
interpolate: True
run_current: 0.8
hold_current: 0.5
stealthchop_threshold: 0

[tmc2209 stepper_z3]
uart_pin: PD15
interpolate: True
run_current: 0.8
hold_current: 0.5
stealthchop_threshold: 0

#[tmc2208 extruder4]
#uart_pin: PD11
#run_current: 0.8
#hold_current: 0.5
#stealthchop_threshold: 999999

########################################
# TMC SPI configuration
########################################

#[tmc2130 stepper_x]
#spi_bus: spi4
#cs_pin: PE6
#diag1_pin: PA14
#run_current: 0.800
#hold_current: 0.500
#stealthchop_threshold: 999999

#[tmc2130 stepper_y]
#spi_bus: spi4
#cs_pin: PE3
#diag1_pin: PA15
#run_current: 0.800
#hold_current: 0.500
#stealthchop_threshold: 999999

#[tmc2130 stepper_z]
#spi_bus: spi4
#cs_pin: PB7
#diag1_pin: PB13
#run_current: 0.800
#hold_current: 0.500
#stealthchop_threshold: 999999

#[tmc2130 extruder]
#spi_bus: spi4
#cs_pin: PB3
#diag1_pin: PA13
#run_current: 0.800
#hold_current: 0.500
#stealthchop_threshold: 999999

#[tmc2130 extruder1]
#spi_bus: spi4
#cs_pin: PD4
#diag1_pin: PC5
#run_current: 0.800
#hold_current: 0.500
#stealthchop_threshold: 999999

#[tmc2130 extruder2]
#spi_bus: spi4
#cs_pin: PD0
#diag1_pin: PB12
#run_current: 0.800
#hold_current: 0.500
#stealthchop_threshold: 999999

#[tmc2130 extruder3]
#spi_bus: spi4
#cs_pin: PD15
#run_current: 0.800
#hold_current: 0.500
#stealthchop_threshold: 999999

#[tmc2130 extruder4]
#spi_bus: spi4
#cs_pin: PD11
#run_current: 0.800
#hold_current: 0.500
#stealthchop_threshold: 999999

########################################
# EXP1 / EXP2 (display) pins
########################################

[board_pins]
aliases:
    # EXP1 header
    EXP1_10=<5V>, EXP1_9=<GND>,
    EXP1_8=PE7,   EXP1_7=PE15,
    EXP1_6=PD8,  EXP1_5=PD9,     # Slot in the socket on the other side
    EXP1_4=PD10,   EXP1_3=PE11,
    EXP1_2=PE10,   EXP1_1=PB2,

    # EXP2 header
    EXP2_10=<5V>, EXP2_9=<GND>,
    EXP2_8=<RST>, EXP2_7=PB11,
    EXP2_6=PA7,   EXP2_5=PE8,       # Slot in the socket on the other side
    EXP2_4=PA4,   EXP2_3=PE9,
    EXP2_2=PA5,   EXP2_1=PA6

# See the sample-lcd.cfg file for definitions of common LCD displays.

# Some alternate glyphs for use with 128x64 LCDs. These are used by
# adding them to your printer.cfg.

# See docs/Config_Reference.md for a description of parameters.

######################################################################
# MKS Mini 12864v3.0 (with neopixel backlight leds)
######################################################################

[display]
lcd_type: uc1701
cs_pin: EXP1_3
a0_pin: EXP1_4
rst_pin: EXP1_5
contrast: 63
encoder_pins: ^EXP2_5, ^EXP2_3
click_pin: ^!EXP1_2
## Some micro-controller boards may require an spi bus to be specified:
#spi_bus: spi
## Alternatively, some micro-controller boards may work with software spi:
spi_software_miso_pin: EXP2_1
spi_software_mosi_pin: EXP2_6
spi_software_sclk_pin: EXP2_2

[output_pin beeper]
pin: EXP1_1

[neopixel fysetc_mini12864]
pin: EXP1_6
chain_count: 3
color_order: RGB
initial_RED: 1.0
initial_GREEN: 1.0
initial_BLUE: 0.0

#####################################################################
# 	Macros
#####################################################################
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

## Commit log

2021-07-30 Upload board picture
2021-09-16 add marlin firmware for voron
    [Configuration.h, Configuration_adv.h]
2021-09-16 Add chinese version of marlin firmware for voron
    [Configuration.h, Configuration_adv.h]
2021-09-18 Upload the manual (Chinese version)
    Upload the manual for using Marlin on VORON V2.4 machine.
2021-09-23 Fix pin map
2021-09-24 Add klipper firmware for monster8
    [generic-mks-monster8.cfg]
2021-09-25 Add voron 2.4 config for monster8 board
    [generic-mks-monster8.cfg, printer.cfg]
2021-10-16 Add .stl files
    [Bottom half.STL, Motherboard bracket.STL, Upper half.STL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]
2022-01-21 Add marlin firmware for V2 board
    [Configuration.h, Configuration_adv.h]
2022-03-02 Update v2.0_002 pin pdf
2022-04-28 Update pin
2022-05-10 add monster8 v2
    [Configuration.h]
2022-07-25 fix printer.cfg file
    [printer.cfg]
2022-07-25 Add v2 klipper config
    [printer_v1.cfg, printer_v2.cfg]
2022-08-16 Update v2.0_002,003 pin map

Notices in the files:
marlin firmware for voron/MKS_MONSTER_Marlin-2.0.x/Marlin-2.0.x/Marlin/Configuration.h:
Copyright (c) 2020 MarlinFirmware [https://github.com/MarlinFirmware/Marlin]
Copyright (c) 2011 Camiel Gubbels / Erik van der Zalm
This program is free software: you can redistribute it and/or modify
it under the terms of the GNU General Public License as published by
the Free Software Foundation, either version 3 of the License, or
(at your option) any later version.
